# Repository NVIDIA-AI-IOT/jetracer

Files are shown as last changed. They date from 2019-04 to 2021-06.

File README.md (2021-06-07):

# JetRacer

> 6/01/2021 - JetPack 4.5.1 based image is updated. It is pre-configured for JetRacer. Detail [here](https://github.com/NVIDIA-AI-IOT/jetracer/blob/master/docs/software_setup.md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).



JetRacer is an autonomous AI racecar using NVIDIA Jetson Nano.  With JetRacer you will

* Go fast - Optimize for high framerates to move at high speeds

* Have fun - Follow examples and program interactively from your web browser

By building and experimenting with JetRacer you will create fast AI pipelines and push the boundaries of speed.

To get started, follow the [setup](#setup) below.

## Cars

There are two different JetRacer cars that you can build.  They differ primarily in size and speed.  Which one to pick depends on your use case

|  Latrax Rally | Tamiya TT02 |
|---|---|
|   |   | 
| 1/18th scale |  1/10th scale |
| Moderate Speed  |  High Speed  |
| ~$400 total build cost | ~$600 total build cost |
| Compact and portable |  Large and easy to modify |
| Soldering required |  No soldering required  |
| Base car pre-assembled | Base car assembly required |

If you have any questions, please reach out by [creating an issue](../..//issues).

## Examples

JetRacer comes with a couple examples to get you up and running.  The examples are in the format of Jupyter Notebooks, which are interactive documents which combine text, code, and visualization.  Once you've completed the notebooks, start tweaking them to create your own racing software!

### Example 1 - Basic motion

In this example you'll learn to progam JetRacer programatically from your web browser.  Learn more in the [examples](docs/examples.md) documentation.



### Example 2 - Road following

In this example, you'll teach JetRacer how to follow a road using AI.  After training the neural network using the [interactive training notebook](notebooks/interactive_regression.ipynb), you'll optimize the model using NVIDIA TensorRT and deploy for a live demo. Learn more in the [examples](docs/examples.md).



## Setup

To get started with JetRacer, follow these steps

1. Order parts from the bill of materials

    - [Latrax version](docs/latrax/bill_of_materials.md) 
    - [Tamiya version](docs/tamiya/bill_of_materials.md) 

2. Follow the hardware setup

    - [Latrax version](docs/latrax/hardware_setup.md) 
    - [Tamiya version](docs/tamiya/hardware_setup.md) 

3. Follow the [software setup](docs/software_setup.md)
4. Run through the [examples](docs/examples.md)

## See also

* [JetBot](http://github.com/NVIDIA-AI-IOT/jetbot) - An educational AI robot based on NVIDIA Jetson Nano

* [JetCam](http://github.com/NVIDIA-AI-IOT/jetcam) - An easy to use Python camera interface for NVIDIA Jetson
* [JetCard](http://github.com/NVIDIA-AI-IOT/jetcard) - An SD card image for web programming AI projects with NVIDIA Jetson Nano
* [torch2trt](http://github.com/NVIDIA-AI-IOT/torch2trt) - An easy to use PyTorch to TensorRT converter

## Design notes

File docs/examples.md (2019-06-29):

# Examples

Follow these examples to get started with JetRacer

> Ensure JetRacer is connected to WiFi and you've note the IP address as in the [software setup](software_setup.md)

## Example 1 - Basic Motion

In this example we'll show how to control JetRacer programatically from a web browser.

1. Navigate to ``http://<jetson_ip_address>:8888``

2. Sign in with the default password ``jetson``
3. Browse to the folder ``~/jetracer/notebooks`` in the Jupyter Lab file browser
4. Run through the notebook ``basic_motion.ipynb``

## Example 2 - Road Following

### Step 1 - Open the interactive trainer

1. Navigate to ``http://<jetson_ip_address>:8888``

2. Sign in with the default password ``jetson``
3. Browse to the folder ``~/jetracer/notebooks`` in the Jupyter Lab file browser
4. Open the notebook ``interactive_regression.ipynb``

### Step 2 - Run the trainer

>  You may want to use ``5W`` mode to prevent the Jetson Nano from drawing to much current and shutting down. Try opening a terminal and entering ``sudo nvpmodel -m1``.

1. In the cell *Task Definition* set ``TASK = 'road_following'`` to set the task name

2. Also set ``CATEGORIES = ['apex']`` to set the class names of the xy target category
3. Execute all of the remaining cells
4. Place the car in different positions, offsets and orientations along the track
5. Imagine the ideal path the car would follow in these positions overlaid on the camera feed
6. Click on the live camera feed as far along that ideal path as possible, such that the robot would not exit the track or collide with an object
7. Repeat this many times (say 50 to start)
8. Train the model for several epochs (say 10 to start) and see how the model performs
9. Iterate!  Try training a model, visualize the output in the live demo, find scenarios where the model is inaccurate and add data for those points, train again...
10. When you want to demo the model, save it to the path ``road_following_model.pth`` and restart the ``interactive_regression.ipynb`` notebook

### Step 3 - Run optimized live demo

1. Open and follow the notebook ``road_following.ipynb``

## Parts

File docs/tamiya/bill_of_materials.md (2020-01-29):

# Bill of Materials - Tamiya TT02

This page lists the parts needed to build JetRacer - Tamiya TT02 version.  After you've received the parts, follow the [hardware setup](hardware_setup.md).



## Jetson Nano

| Part | Quantity | Cost | URL | Notes |
|---|:---:|:---:|-----|---|
| Jetson Nano | 1 | $99.00 | [NVIDIA](https://developer.nvidia.com/buy-jetson?product=jetson_nano), [Amazon](https://amzn.to/2K36TPl) |  |
| Micro SD Card | 1 | $11.99 | [Amazon](https://amzn.to/2Mohzd1) | Must be at least 32GB |
| USB Battery | 1 | $13.99 | [Amazon](http://amzn.com/B07KPCKCYG/) | Must provide at least 5V @ 2A |
| USB A -> 2.1mm Barrel Cable | 1 | $7.00 | [Amazon](https://amzn.to/2SMmu8A) |  |
| 5V @ 4A Barrel Plug Power Supply | 1 | $14.95 | [Adafruit](https://www.adafruit.com/product/1466) | 2.1mm Iinner diameter |
| Jumper Caps Pack | 1 | $5.09 | [Amazon](https://amzn.to/2LP96QI) | 2.54mm pitch |

## Chassis

| Part | Quantity | Cost | URL | Notes |
|---|:---:|:---:|-----|---|
| RC Car | 1 | $118.99 | [Amazon](https://amzn.to/2LUn3gj), [Hobbytown](https://www.hobbytown.com/tamiya-nsx-tt02-4wd-on-road-tam58634/p508229), [Tamiya](https://www.tamiyausa.com/shop/110-4wd-shaft-drive-road-tt/rc-nsx/tt-02/) | Tamiya NSX TT-02 assembly kit
| Servo | 1 | $15.98 | [Amazon](https://amzn.to/2LS781O) | Futaba S3004 Standard Ball Bearing Servo |
| TX RX Combo | 1 | $129.99 | [Amazon](https://amzn.to/2yoyWC5) | Futaba 3PV 3ch 2.4GHz transmitter and receiver module set |
| RC battery pack | 1 | $39.99 | [Amazon](https://amzn.to/31330PW) | Tenergy 7.2V 3000mAh NiMH (2-pack) |
| RC battery charger | 1 | $20.99 | [Amazon](https://amzn.to/2GHi3ay) | Tenergy Universal RC Battery Charger |
| 3d-printed base board | 1 |  | [STL file](../../assets/tamiya_tt02/jetracer_tamiya_tt02_base_board.stl) | Can be printed purchased at [Donkey Car](https://store.donkeycar.com/products/nvidia-jetracer-3d-printed-parts) Store |
| 3d-printed camera mount | 1 |  | [STL file](../../assets/jetracer_cam_mount.stl) | Can be printed purchased at [Donkey Car](https://store.donkeycar.com/products/nvidia-jetracer-3d-printed-parts) Store |

## Jig

| Part | Quantity | Cost | URL | Notes |
|---|:---:|:---:|-----|---|
| 3d-printed jig plate | 1 |  | [STL file](../../assets/tamiya_tt02/jetracer_tamiya_tt02_drill_jig.stl) | to help drill holes on RC car chassis |

## Electronics

| Part | Quantity | Cost | URL | Notes |
|---|:---:|:---:|-----|---|
| PWM Servo Motor Driver | 1 | $6.99 | [Amazon](https://amzn.to/317xYqr) |
| RC Servo Multiplexer | 1 | $9.95 | [Pololu](https://www.pololu.com/product/2806) | |
| Servo Extension Cable Pack | 1 | $5.91 | [Amazon](https://amzn.to/2SMnkSM) | Male to Male, 10cm |
| Jumper Wire Pack | 1 | $6.98 | [Amazon](https://amzn.to/319x9NT) | Female to Female, > 10cm | |

## Wi-Fi

| Part | Quantity | Cost | URL | Notes |
|---|:---:|:---:|-----|---|
| Wi-Fi Card | 1 | $18.95 | [Amazon](https://amzn.to/319d6z3), [NewEgg](https://www.neweggbusiness.com/Product/Product.aspx?Item=9SIV21M85N2699) |  |
| Wi-Fi Antenna kit | 1 | $8.99 | [Amazon](https://amzn.to/2SPft6U) | IPEX MHF4 connectors |

## Camera

You need a wide angle camera for JetRacer.  Pick an option and order the parts listed.

### Option 1 - Wide angle Leopard Imaging camera

| Part | Quantity | Cost | URL | Notes |
|---|:---:|:---:|-----|---|
| Camera | 1 | $29 | [Leopard Imaging](https://leopardimaging.com/product/li-imx219-mipi-ff-nano/) | Select wide angle (**H145**) option |

### Option 2 - Raspberry Pi Camera V2 + Wide angle attachment

| Part | Quantity | Cost | URL | Notes |
|---|:---:|:---:|-----|---|
| Camera | 1 | $23.90 | [Amazon](https://amzn.to/2MSi6lL), [Adafruit](http://adafru.it/3099) | Raspberry Pi Camera V2 |
| Wide angle attachment | 1 | $18.99 | [Amazon(1)](https://amzn.to/2SPNKDu), [Amazon(2)](https://amzn.to/2SPOfgQ), [eBay](https://ebay.us/Fz7HGd) | 160-degree FoV |

## Assembly Hardware

| Part | Quantity | Cost | URL | Notes |
|---|:---:|:---:|-----|---|
| M3x45mm Standoff Pack | 1 | $10.69 | [Amazon](https://amzn.to/2LPuZ20) | To support 3d-printed base plate |
| M3 Universal Screw Pack | 1 | $12.94 | [Amazon](https://amzn.to/2LNGt6q) | 4x M3x8mm screws, 4x M3 flat head screws needed for 4 standoffs |
| M2x8mm Screw Pack | 1 | $6.39 | [Amazon](https://amzn.to/312PTOK) | Mounts accessories to 3D printed base plate.  18 screws needed per car |
| Battery Strap Pack | 1 | $6.98 | [Amazon](https://amzn.to/317zoRN) | 1 needed per car |

## Next

Follow the [hardware setup](hardware_setup.md).

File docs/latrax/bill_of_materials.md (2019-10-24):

# Bill of Materials

This page lists the parts needed to build JetRacer - Latrax Rally version.  After you've received the parts, follow the [hardware setup](hardware_setup.md).



## Jetson Nano

| Part | Quantity | Cost | URL | Notes |
|---|:---:|:---:|-----|---|
| Jetson Nano | 1 | $99.00 | [NVIDIA](https://developer.nvidia.com/embedded/buy/jetson-nano-devkit) |  |
| Micro SD Card | 1 | $13.99 | [Amazon](https://amzn.to/2Us6bOv) | Must be at least 32GB |
| USB Battery | 1 | $15.95 | [Amazon](https://www.amazon.com/5000-mah-Attom-Tech-Portable-Emergency/dp/B07MNWPFG8/) | Must provide at least 5V @ 2A |
| USB A -> 2.1mm Barrel Cable | 1 | $7.00 | [Amazon](https://www.amazon.com/gp/product/B075112RM6/) |  |
| 5V @ 4A Barrel Plug Power Supply | 1 | $14.95 | [Adafruit](https://www.adafruit.com/product/1466) | 2.1mm Iinner diameter |
| Jumper Caps Pack | 1 | $5.09 | [Amazon](http://amzn.com/B077957RN7/) | 2.54mm pitch |

## Chassis

| Part | Quantity | Cost | URL | Notes |
|---|:---:|:---:|-----|---|
| RC Car | 1 | $109.95 | [HobbyTown](https://www.hobbytown.com/traxxas-latrax-rally-1-18-4wd-rtr-rally-racer-green-tra75054-5-grn/p630138), [Amazon](http://amzn.com/B06W57XLRW) | Traxxas LaTrax Rally 1/18 4WD w/ 2.4GHz radio |
| 3d-printed base board | 1 |  | [STL file](../../assets/latrax_rally/jetracer_latrax_base_board.stl) | Can be printed purchased at [Donkey Car](https://store.donkeycar.com/products/nvidia-jetracer-3d-printed-parts) Store |
| 3d-printed camera mount | 1 |  | [STL file](../../assets/jetracer_cam_mount.stl) | Can be printed purchased at [Donkey Car](https://store.donkeycar.com/products/nvidia-jetracer-3d-printed-parts) Store |

## Electronics

| Part | Quantity | Cost | URL | Notes |
|---|:---:|:---:|-----|---|
| PWM Servo Motor Driver | 1 | $6.99 | [Amazon](http://amzn.com/B01D1D0CX2/) | PCA9685 |
| RC Servo Multiplexer | 1 | $9.95 | [Pololu](https://www.pololu.com/product/2806) | |
| Servo Extension Cable Pack | 1 | $5.91 | [Amazon](http://amzn.com/B00P6JJFIS/) | Male to Male, 10cm |
| Jumper Wire Pack | 1 | $6.98 | [Amazon](http://amzn.com/B01EV70C78/) | Female to Female, > 10cm | |
| Manual Override Switch Pack | 1 | $10.99 | [Amazon](https://www.amazon.com/gp/product/B07L74MMG8/) | |

## Wi-Fi

| Part | Quantity | Cost | URL | Notes |
|---|:---:|:---:|-----|---|
| Wi-Fi Card | 1 | $18.95 | [Amazon](https://amzn.to/2WKEkum), [NewEgg](https://www.neweggbusiness.com/Product/Product.aspx?Item=9SIV21M85N2699) |  |
| Wi-Fi Antennas | 2 | $5.06 | [Arrow](https://www.arrow.com/en/products/2042811100/molex) |  |

## Camera

You need a wide angle camera for JetRacer.  Pick an option and order the parts listed.

### Option 1 - Wide angle Leopard Imaging camera

| Part | Quantity | Cost | URL | Notes |
|---|:---:|:---:|-----|---|
| Camera | 1 | $29 | [Leopard Imaging](https://leopardimaging.com/product/li-imx219-mipi-ff-nano/) | Select wide angle (**H145**) option |

### Option 2 - Raspberry Pi Camera V2 + Wide angle attachment

| Part | Quantity | Cost | URL | Notes |
|---|:---:|:---:|-----|---|
| Camera | 1 | $23.90 | [Amazon](https://amzn.to/2MSi6lL), [Adafruit](http://adafru.it/3099) | Raspberry Pi Camera V2 |
| Wide angle attachment | 1 | $18.99 | [Amazon(1)](https://amzn.com/B07HMXJ9Y1), [Amazon(2)](https://amzn.com/B07HF81BVL/), [eBay](https://ebay.us/Fz7HGd) | 160-degree FoV |

## Assembly Hardware

| Part | Quantity | Cost | URL | Notes |
|---|:---:|:---:|-----|---|
| M2x6mm Screw Pack | 1 | $13.53 | [Amazon](https://www.amazon.com/gp/product/B01FXGHO2M/) | Mounts accessories to 3D printed base plate.  12 screws needed per car |
| M3x20mm Standoff Pack | 1 | $6.99 | [Amazon](https://www.amazon.com/dp/B072DVGWHZ/ref=cm_sw_su_dp) | Mounts 3D printed base plate to RC chassis. 4 standoffs needed per car |
| M2x38mm Screw Pack | 1 | $11.99 | [Amazon](http://amzn.com/B07CHJBK6F) | 2 needed per car |
| M2x30mm Screw Pack | 1 | $7.96 | [Amazon](https://www.amazon.com/dp/B015A31EVK/ref=cm_sw_su_dp) | 2 needed per car |
| Adhesive Pads Pack | 1 | $6.98 | [Amazon](https://www.amazon.com/gp/product/B001KYSAN4/) | 4 needed per car |

## Next

Follow the [hardware setup](hardware_setup.md).

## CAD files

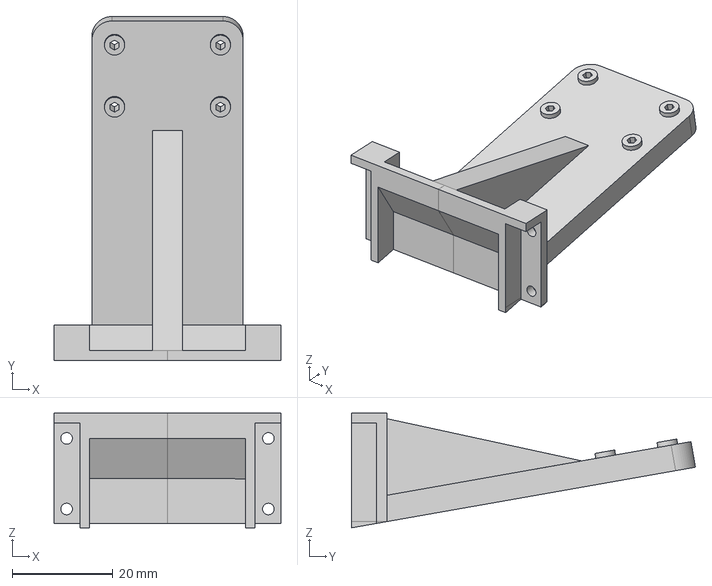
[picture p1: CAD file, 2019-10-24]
assets/jetracer_cam_mount.step
45.0 x 68.2 x 22.7 mm

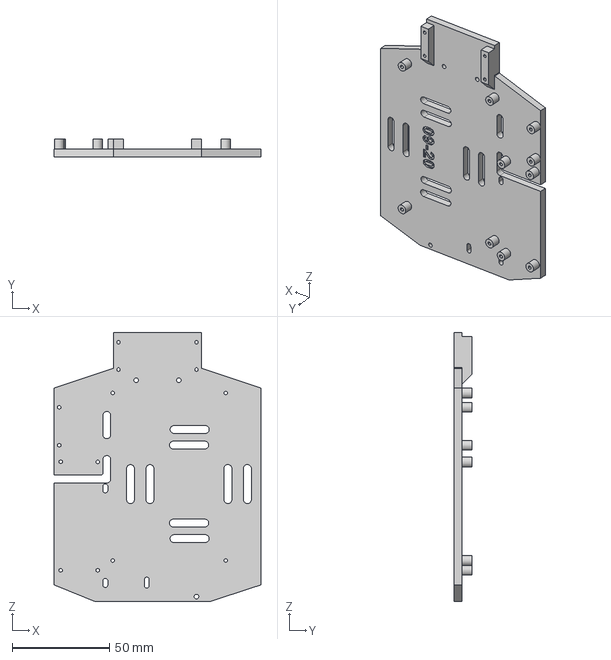
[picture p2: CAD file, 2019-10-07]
assets/latrax_rally/jetracer_latrax_base_board.step
106.0 x 9.00 x 138.0 mm

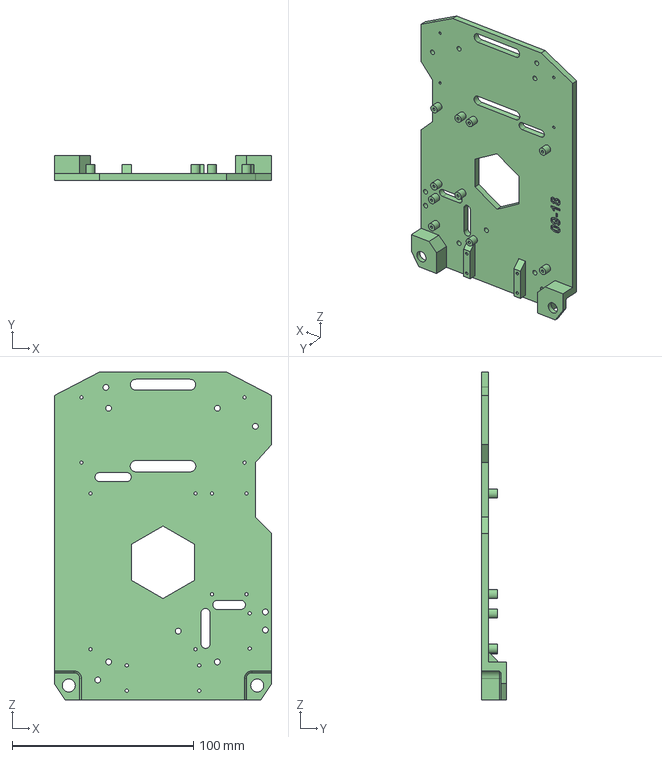
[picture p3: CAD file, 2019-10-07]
assets/tamiya_tt02/jetracer_tamiya_tt02_base_board.step
120.0 x 14.0 x 181.0 mm

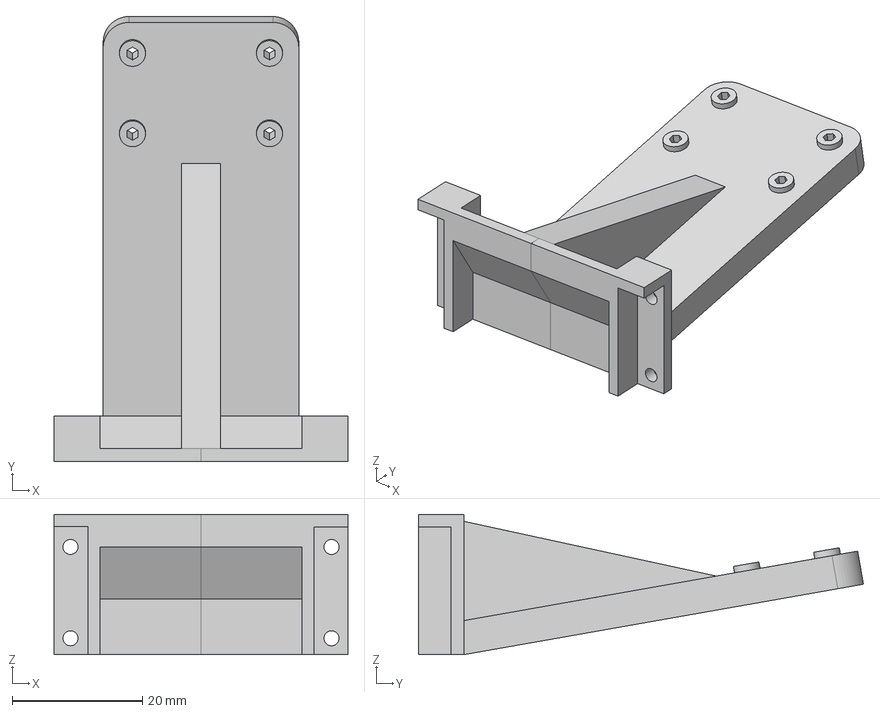
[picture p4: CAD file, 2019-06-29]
assets/latrax_rally/jetracer_latrax_cam_mount.step
45.0 x 68.2 x 21.5 mm

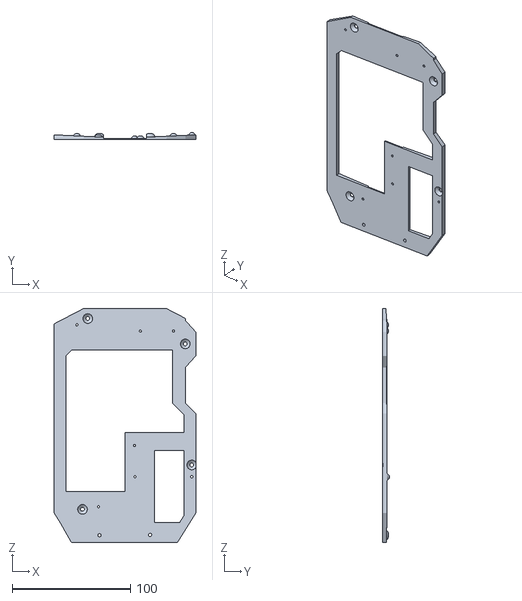
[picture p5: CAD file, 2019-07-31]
assets/tamiya_tt02/jetracer_tamiya_tt02_drill_jig.stl
120.0 x 6.00 x 198.0

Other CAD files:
assets/jetracer_cam_mount.iges
assets/jetracer_cam_mount.stl
assets/latrax_rally/jetracer_latrax_base_board.iges
assets/latrax_rally/jetracer_latrax_base_board.stl
assets/latrax_rally/jetracer_latrax_cam_mount.iges
assets/latrax_rally/jetracer_latrax_cam_mount.stl
assets/tamiya_tt02/jetracer_tamiya_tt02_base_board.iges
assets/tamiya_tt02/jetracer_tamiya_tt02_base_board.stl

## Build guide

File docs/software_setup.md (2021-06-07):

# Software Setup

> If you have built a 3rd-pary Jetracer kit (other than our DIY vehicles based on Latrax Rally or Tamiya TT-02), the following method (and the SD card images) may not work. <br> **Please check the manufacture's instruction on its kit's specific software setup.**

After finishing these steps, you'll be all set to program JetRacer.  Once you're finished, run through the [examples](examples.md).

## Step 1 - Flash micro SD card

1. Download a JetCard SD card image listed in below table onto a Windows, Linux or Mac *desktop machine*
2. Insert a 32GB+ SD card into the desktop machine
3. Using [Etcher](https://www.balena.io/etcher/) select the downloaded zip file and flash it onto the SD card
4. Remove the SD card from the desktop machine

### Latest Release (** **but not yet fully verified** ** )

> Please note, the password for the pre-built SD card is ``jetson``

| Platform | Board revision | JetPack Version | Download | MD5 Checksum |
| --- | --- | --- | --- |--- |
| Jetson Nano (4GB) | `A02` and `B01` | 4.5.1 |  [jetcard_nano-4gb-jp451.zip](https://drive.google.com/file/d/1aPbzQ0_Uja0jVD48oZUAuYYAz10JgbZu/view?usp=sharing) | 3195c91e6069c0418ec3c9736d130d01 |

### Old Release

> Please note that this image is only for the older `A02` revision of Jetson Nano board, which has only one camera (CSI) connector onboard.

| Platform | Board revision | JetPack Version | Download | MD5 Checksum |
| --- | --- | --- | --- |--- |
| Jetson Nano (4GB) | `A02` | 4.2|  [jetcard_v0p0p0.zip](https://drive.google.com/open?id=1wXD1CwtxiH5Mz4uSmIZ76fd78zDQltW_) | f7b635a651e4a2228e3812360cce74e3 | 

## Step 2 - Power on and connect over USB

1. Insert the configured SD card into the Jetson Nano module

2. Power on by plugging the USB barrel plug adapter into the USB battery pack
3. Connect your Windows, Linux, or Mac machine to the Jetson Nano via micro USB

4. On your Windows, Linux, or Mac machine, open a browser and navigate to ``192.168.55.1:8888``
5. Sign in using the default password ``jetson``

## Step 2 - Connect JetRacer to WiFi

1. Open a terminal in Jupyter Lab by clicking ``File`` -> ``New`` -> ``Terminal``

2. In the terminal, type the following command to list available WiFi networks, and find the ``ssid_name`` of your network.

    ```bash
    sudo nmcli device wifi list
    ```
3. Connect to  the selected WiFi network

    >  It should be on the same network that you will be webprogramming from

    ```bash
    sudo nmcli device wifi connect <ssid_name> password <password>
    ```
4. Note down the WiFi IP address (``inet``) of the WiFi interface ``wlan0`` returned by the following command.  We'll call this ``jetson_ip_address``
    
    ```bash
    ifconfig
    ```

## Step 4 - Connect to JetRacer over WiFi

1. Unplug the micro USB cable from the Jetson Nano

2. Close the previous Jupyter Lab browser tab
3. Open a new browser tab and navigate to ``http://<jetson_ip_address>:8888``
4. Sign in with the password ``jetson``
    
## Step 5 - Install Python packages

>  If you're using the latest JetCard image (targeting JetPack 4.5.1 or later), you can skip this step.  The latest JetCard image comes with these packages pre-installed.

1. Open a terminal and call the following to install the [JetCam](http://github.com/NVIDIA-AI-IOT/jetcam) Python package.

    ```bash
    cd $HOME
    git clone https://github.com/NVIDIA-AI-IOT/jetcam
    cd jetcam
    sudo python3 setup.py install
    ```
    
2. Execute the following command to install the [torch2trt](http://github.com/NVIDIA-AI-IOT/torch2trt) Python package

    ```bash
    cd $HOME
    git clone https://github.com/NVIDIA-AI-IOT/torch2trt
    cd torch2trt
    sudo python3 setup.py install
    ```
    
2. Execute the following in a terminal to install the [JetRacer](http://github.com/NVIDIA-AI-IOT/jetracer) package
 
     ```bash
     cd $HOME
     git clone https://github.com/NVIDIA-AI-IOT/jetracer
     cd jetracer
     sudo python3 setup.py install
     ```
 
## Step 6 - Set the Jetson Nano to 5W mode

To prevent the Jetson Nano from drawing more power than the battery can supply, we set it to 5W mode

1. Open a terminal and call the following to set 5W mode

    ```bash
    sudo nvpmodel -m1
    ```
    
## Next

Next, follow run through the [examples](examples.md).

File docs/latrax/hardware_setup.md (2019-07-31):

# Hardware Setup

Follow these instructions to build JetRacer - Latrax Rally version.  After you've finished, move on to the [software setup](../software_setup.md).

## Tools

* Phillips screwdriver set
* Hex screwdriver
* Soldering iron
* Drill with 3mm and 6mm drill bits
* Pliers
* Wire strippers

## Phase 1 - Car disassembly
### Step 1 - Remove shroud from car






1. Remove the 4 pins securing the shroud

2. Remove the shroud from the chassis

### Step 2 - Remove ESC and RC receiver from car










1. Remove the two screws securing the electronics hub to the chassis

2. Pry the electronics hub from the chassis
3. Remove the ESC and RC receiver from the electronics hub
4. Disconnect the two servo cables from the RC receiver
5. Remove the foam adhesive from the RC receiver

## Phase 2 - Car wiring
### Step 1 - Connect Jetson to servo driver






1. Select 4 female-to-female jumper cables from the bundle

2. Attach the jumpers to the servo driver pins ``VCC`` (white), ``SDA`` (gray), ``SCL`` (purple) and ``GND`` (black)
3. Attach the other end of the jumpers to the Jetson Nano pins ``3.3V`` (white), ``3`` (gray), ``5`` (purple) and ``GND`` (black)

### Step 2 - Connect servo driver to multiplexer








1. Connect channel ``0`` on the servo driver to channel ``S1`` on the multiplexer

    > Pay attention to the orientation of the cable for these steps!
    
2. Connect channel ``1`` on the servo driver to channel ``S2`` on the multiplexer

### Step 3 - Connect RC receiver to multiplexer










1. Connect channel ``3`` on the RC receiver to ``SEL`` on the multiplexer

2. Connect channel ``2`` on the RC receiver to ``M2`` on the multiplexer
3. Connect channel ``1`` on the RC receiver to ``M1`` on the multiplexer

### Step 4 - Connect multiplexer to ESC and servo








1. Connect the servo to ``OUT1`` on the multiplexer

2. Connect the ESC to ``OUT2`` on the multiplexer

## Phase 3 - Car assembly

### Step 1 - Mount ESC to base plate






1. Attach ESC to the base plate as indicated

    > Notice the two slots on the base plate for the ESC
    
2. Press down firmly to secure the ESC

### Step 2 - Mount RC receiver to base plate




1. Attach the RC receiver to the base plate as indicated

2. Press down firmly to secure the RC receiver

### Step 3 - Expose screw holes used to mount base plate







1. Remove the 4 screws indicated to expose holes used to mount the base plate

### Step 4 - Mount base plate to RC car










1. Select 4 ``M3x20mm standoffs``, 2 ``M2x38mm`` screws and 2 ``M2x30mm`` screws

2. Attach the base plate to the RC car chassis as indicated
3. Fasten the base plate using a hex screwdriver

### Step 5 - Route servo motor wire through base plate





> If the servo cable is not long enough to reach around the base plate, please route it as follows

1. Remove the servo cable from ``OUT1`` on the multiplexer that we attached previously

2. Route the servo wire through the slot base plate as indicated
3. Reconnect the servo cable to ``OUT1`` on the multiplexer

### Step 6 - Mount components to base plate







1. Select 10 of the ``M2x6mm`` screws

2. Fasten the multiplexer to the base plate
3. Fasten the servo driver to the base plate
4. Fasten the Jetson Nano to the base plate

### Step 7 - Connect WiFi card












1. Attach the two antennas to the WiFi card

2. Remove the Jetson Nano module from the developer kit board as indicated
3. Remove the M2 connector securing screw on the developer kit base board
4. Insert the WiFi card into the M2 connector slot
5. Reattach the screw to secure the WiFi card
6. Reattach the Jetson Nano module to the developer kit board

### Step 8 - Connect camera








1. Attach the camera to the Jetson Nano developer kit as indicated

    > Be careful when loosing the camera connector to not break it
    
2. Attach the camera mount to the base plate using 4 ``M2x6mm`` screws
3. Attach the camera to the camera mount using 4 ``M2x6mm`` screws

### Step 9 - Mount USB battery pack





1. Attach the USB battery pack to the underside of the base plate as indicated

### Step 10 - Attach USB barrel plug




1. Attach the 2 pin jumper to ``J48`` on the Jetson Nano developer kit to enable barrel plug power

2. Insert the barrel plug into the Jetson Nano developer kit

    > Before powering on, you'll need to follow the [software setup](../software_setup.md) to configure the SD card
    
## Phase 4 - RC transmitter modification

### Step 1 - Dissasmble radio










1. Remove the 5 screws securing radio halves with a phillips screwdriver

2. Peel off the radio stick joining the two halves
3. Place the radio sticker on one half of the radio
4. Remove the battery cover
5. Separate the radio into halves

### Step 2 - Remove trim / reset PCB





1. Remove screw securing the trim/reset PCB

2. Carefully sliding the wires out of the securing clip and pull the PCB to the side

### Step 3 - Drill hole for manual override switch





1. Mark the RC transmitter as indicated by the screwdriver tip

2. Using a ``6mm`` diameter drill bit, drill a hole through the marked location

### Step 4 - Drill hole for switch key






1. Temporarily insert the switch into the RC transmitter

2. Place the key washer on the other side of the transmitter
3. Mark the RC transmitter at the location of the screwdriver tip
4. Using a roughly ``2.5mm - 3.5mm`` drill bit, drill a hole through the marked location

### Step 5 - Fasten manual switch to RC transmitter







1. Re-insert the manual override switch into the hole

2. Place the keyed washer and nut back on the switch
3. Fasten the switch to the RC transmitter using pliers

### Step 6 - Solder switch to RC transmitter PCB










1. Cut the wires roughly at the length indicated

    > Ensure you cut the wires with enough length to reach the solder pads

2. Strip the wires as indicated
2. Apply solder to the two pads indicated
3. Apply solder to the stripped wire leads
4. Using pliers, hold the wires against the pads indicated and apply heat with the soldering iron

### Step 7 - Reassemble RC transmitter







1. Re-attach the halves of the RC transmitter

2. Fasten the halves using the original screws
3. Insert the 4 ``AA`` batteries, and apply the battery cover

## Hardware setup complete!



## Next

Next, follow the [software setup](../software_setup.md).

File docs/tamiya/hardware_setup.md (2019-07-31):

# Hardware Setup - Tamiya TT02

Follow these instructions to build JetRacer - Tamiya TT02 version.  After you've finished, move on to the [software setup](../software_setup.md).

## Tools

* Phillips screwdriver set
* Hex screwdriver
* Drill with 3mm and 6mm drill bits
* Countersink drill bit
* Pliers
* Wire strippers

## Phase 1 - TT-02 chassis setup
### Step 1 - Drilling mount holes to TT-02 chassis
> [Tips] It is better to perform this drilling before assembling the Tamiya TT-02 parts






1. Attach the jig on TT-02's "Lower deck" chassis ([Item #51532](https://www.tamiyausa.com/shop/spare-parts/rc-tt02-lower-deck/))

2. Align the jig to chassis holes. Use tapes to secure it
3. Use a ``3mm`` drill bit to drill 4 holes 

### Step 2 - Countersink 

> [Tips] Use of independent countersink drill bit (as opposed to the integrated one in the photo) is recommended.




1. Use countersink drill bit to make countersinks for flathead screw

2. Do this for all 4 holes

### Step 3 - Shaving motor cover




1. Use ``6mm`` drill bit to shave off part of motor cover part

2. Make sure it now has enough room for ``M3x45mm`` standoff to sit on the countersink hole you made on prior step

### Step 4 - Attaching standoffs on chassis 







1. Attach ``M3x45mm`` standoffs on "Lower deck" chassis with M3x8mm flat-head screws

2. Do this on all 4 holes
3. Do not tighten screws yet

## Phase 2 - Mounting components on base plate
### Step 1 - Multiplexer






1. Use 2x ``M2x8mm`` tapping screws to mount the multiplexier on the base plate

### Step 2 - Servo Motor Driver





1. Use 4x ``M2x8mm`` tapping screws to mount Servo Motor Driver on the base plate

### Step 3 - Jetson Nano Developer Kit





1. Use 4x ``M2x8mm`` tapping screws to mount Servo Motor Driver on the base plate

### Step 4 - IMX219 camera on Camera Mount





1. Use 4x ``M2x8mm`` tapping screws to attach camera to the camera mount

### Step 5 - Wi-Fi antennas







1. Place SMA anntena connector through the base plate hole

2. Put lock washer and split washer, and use the nut to tighten



## Phase 3 - Wiring

### Step 1 - Camera to Jetson Nano







1. Attach the camera to the Jetson Nano developer kit as indicated

    > Be careful when loosing the camera connector to not break it
2. Attach the camera to the camera mount using 4x ``M2x8mm`` screws
3. Attach the camera mount to the base plate using 4x ``M2x8mm`` screws

### Step 2 - Jetson Nano to Servo Motor Driver






1. Select 4 female-to-female jumper cables from the bundle

2. Attach the jumper wires to the Jetson Nano pins ``3.3V`` (red), ``3`` (orange), ``5`` (yellow) and ``GND`` (brown)
3. Attach the jumpers to the servo driver pins ``VCC`` (red), ``SDA`` (orange), ``SCL`` (yellow) and ``GND`` (brown)

### Step 3 - Servo Motor Driver to multiplexer





1. Connect channel ``0`` on the servo driver to channel ``S1`` on the multiplexer

    > Pay attention to the orientation of the cable for these steps!
2. Connect channel ``1`` on the servo driver to channel ``S2`` on the multiplexer

### Step 4 - Wi-Fi antenna to M.2 card





1. Attach the two antennas to the Wi-Fi card

### Step 5 - Wi-fi M.2 card to Jetson Nano










1. Remove the Jetson Nano module from the developer kit board as indicated

2. Remove the M.2 connector securing screw on the developer kit base board
3. Insert the Wi-Fi card into the M.2 connector slot
4. Reattach the screw to secure the Wi-Fi card

### Step 6 - USB Battery to Jetosn Nano







1. Attach the 2 pin jumper to ``J48`` on the Jetson Nano developer kit to enable barrel plug power

2. Insert the USB plug into the powerbank
3. Insert the barrel plug into the Jetson Nano Developer Kit
4. Use battery strap to fasten the battery on the base plate



### Step 7 - RX (RC receiver) to mulptiplexer






1. Connect ``CH3`` on the RC receiver to ``SEL`` on the multiplexer

2. Connect ``CH2`` on the RC receiver to ``M2`` on the multiplexer
3. Connect ``CH1`` on the RC receiver to ``M1`` on the multiplexer

### Step 8 - RC's ESC and servo to mulptiplexer 






1. Connect the RC servo to ``OUT1`` on the multiplexer

2. Connect the RC ESC to ``OUT2`` on the multiplexer

## Phase 4 - Final Assembly





1. Use 4x ``M3x8mm`` screws to attach base plates to the ``M3x45mm`` standoffs
2. Tighten the bottom flathead screws along with top ``M3x8mm`` screws
3. Attach the antenna to the SMA connectors

## Hardware setup complete!



## Next

Next, follow the [software setup](../software_setup.md).

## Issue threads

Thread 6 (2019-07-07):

Criteria for choosing the RC car

abhinav-upadhyay, 2019-07-07:
Hi,

This is not really an issue but a query. Did you choose the Traxxas LaTrax Rally car specifically for a particular reason, such as the 3d printed base board would fit well with it, or you knew that it was hackable? I am asking because the Traxxas RC cars are not available in India and importing it costs 3x more. There are other RC cars with similar specs (1:18 scale, 2.4 GHz radio, 4WD), such as [this](https://www.amazon.in/Sky-Zone-Waterproof-Controlled-Crawler/dp/B07JK3J437/).

The Donkey car is also a relatively affordable option. I would appreciate if you could give any opinion on this, I have never played with RC cars and haven't done any hardware hacking before.

tokk-nv, 2019-07-08:
Hi Abhinav,
Thank you for your question.

We chose Latrax Rally car mainly because it was hackable and small (being small is nice when it comes to demonstrating in a small space).
But you should be able to use other cars, as long as **they expose Servo and ESC controls through the standard 3-pin "Servo" connectors**.
So anything used in Donkey Car should work.

Our observation is that, once the RC car gets smaller than 1/10 scale, it uses what people call 3-in-1 controller, which combines the radio receiver (RX), the servo controller and the ESC in one unit.
This makes it very difficult to hack, as you cannot simply plug the cables from Servo and ESC to the PCA9685 board.
You can tell the car is using 3-in-1 design by finding the 5-wire cable coming out from the servo, like the one on Amazon you suggested.
Availability of the upgrade/replacement parts is also a good indication that the car is hackable.

I think you will have a better chance if you go for 1/10 scale and look in the hobby section rather than the toy section. (Perhaps you can find some relevant info on a forum like [this](http://www.rcindia.org/index.php)?)
I hope you will find a reasonably priced car for your project, and please share with us if you find a good one.

jasonlililililili, 2020-10-25:
May I ask which component has signal input and power output? Because I have no idea which component (RC reveiver? PCA9685? Servo Motor Driver? RC Servo? or the RC ESC?) should be connected to the battery.
Thank You!

krissdap, 2020-11-17:
Battery sends power to ESC.

In normal RC car, ESC connects to RC receiver, sends the power, and the receiver shares the power the steering servo connected to it.

In JetRacer, you have the servo multiplexer in the middle. And you power the Jetson Nano with USB power bank.

Of course you can also power each component in other ways if you are adventurous. :)

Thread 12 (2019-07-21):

VCC or V+?

zlite, 2019-07-21:
In this step of the instructions, you say to connect to VCC but the picture shows the connection to V+. Which is right?
https://user-images.githubusercontent.com/25759564/60315002-a56b1000-9919-11e9-8a53-2d941cc1b139.JPG

zlite, 2019-07-21:
If you plug it into V+ bad things happen! Nukes carrier board, wifi, etc. Yikes

jaybdub, 2019-07-21:
Hi Chris,

Thanks for pointing this out!  You're right, it's supposed to be VCC as stated.

We had this in right in an earlier shoot, I've updated to use the correct image.  You can find the change here

https://github.com/NVIDIA-AI-IOT/jetracer/blob/master/docs/hardware_setup.md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

Sorry for the confusion, I hope this didn't cause too much trouble.   Please reach out if you find anything else!

Thanks,
John

Closed 2022-07-18.

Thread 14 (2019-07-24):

Can you use C++ and ROS to control the car

ghost, 2019-07-24:
Seems you have to run Python via WIFI to control the car. What if you do not have WIFI? Can you run C++ and ROS to control the car?

jaybdub, 2019-07-27:
Hi Deeprun,

Thanks for reaching out!

>  What if you do not have WiFi?

You actually don't need WiFi.  This is a convenience so you can easily access the programming environment for rapid prototyping.  If you don't have WiFi, you can connect directly over micro USB, and access the web programming environment at ``192.168.55.1:8888``.  Or you could always open the a web browser on the Jetson Nano itself.  This would consume memory on the Nano though.

The examples are Jupyter notebooks (which require a web browser), but you can still operate the robot in plain Python (ie ``racecar.throttle = 0.3`` still works.

> Can you run in C++ and ROS to control the car?

We don't have a C++ library or ROS interface for JetRacer.  To create one, the primary effort would be in interfacing with the ``PCA9865`` servo driver chip to control the steering / throttle.  Perhaps there are C++ libraries (or maybe even ROS) for this purpose.

Please let me know if you have any other questions.

Best,
John

UberWagen, 2020-08-14:
> We don't have a C++ library or ROS interface for JetRacer. To create one, the primary effort would be in interfacing with the `PCA9865` servo driver chip to control the steering / throttle. Perhaps there are C++ libraries (or maybe even ROS) for this purpose.

Old thread, but I'm in the process of trying it. [This guy](https://github.com/dheera/ros-pwm-pca9685) did write a ROS driver for the 9865 if anyone finds this in the future.

Closed 2022-07-18.

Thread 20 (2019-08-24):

RC transmitter modification for tamiya version

hygradme, 2019-08-24:
Hi, I made JetRacer of tamiya version.

Then, I followed the instruction in [docs/examples.md](https://github.com/NVIDIA-AI-IOT/jetracer/blob/master/docs/examples.md) Example 1 - Basic Motion.
When I run the line of car.steering = 0.3 in [notebooks/basic_motion.ipynb](https://github.com/NVIDIA-AI-IOT/jetracer/blob/dev-stl/notebooks/basic_motion.ipynb), my car doesn't response.
The comment in the notebook said:
> If the car does not respond, it may still be in ``manual`` mode.  Flip the manual override switch on the RC transmitter.

However, my RC transmitter ( which is TTU-08 also in the photo of [docs/tamiya/bill_of_materials.md](https://github.com/NVIDIA-AI-IOT/jetracer/blob/master/docs/tamiya/bill_of_materials.md)) doesn't have override switch.

It seems like the hardware setup for latrax (at the Phase 4 of [docs/latrax/hardware_setup.md](https://github.com/NVIDIA-AI-IOT/jetracer/blob/dev-stl/docs/latrax/hardware_setup.md)) has RC transmitter modification.
Does tamiya version also have to do same modification like latrax version to make it ``manual`` mode?

romybompart, 2019-08-26:
Hi. I was reading, it uses channel 3 switch to change from manual to "Nvidia" mode.

Channel 3 is connected to SEL which is the input of the PIC10 at the PWM multiplexer. So that pin detects a pwn threshold to let channel M1 to M4 or S1 to S4 pass to OUT1 to OUT4 respectively.

In this manual you will see what is channel 3 switch:

manuals.hobbico.com › futPDF
Resultados de la Web
1M23N31504 - You have reached ftp.hobbico.com

If this does not work for you you can by pass the multiplexer and connect the PCA PWM driver ch0 to the steering wheel servo and ch1 to the ESC, but you won't have command on the car by your transmitter.

Let me know whatever you got.

hygradme, 2019-08-26:
Thank you for your advice.

I think I didn't have enough knowledge about RC transmitter.
My  [Tamiya RC Transmitter](https://www.amazon.com/Fine-Electric-Drive-Model-tamiya/dp/B0077K0WM2) has only 2ch which cannot send SEL signal to the receiver.

I bought combo version of NSX RC car with Tamiya TT02 and RC transmitter which is different from the one in [bill of materials](https://github.com/NVIDIA-AI-IOT/jetracer/blob/master/docs/tamiya/bill_of_materials.md).
I should have bought Futaba 3PV 3ch 2.4GHz transmitter.

As you told me, I bypass the multiplexer and switch "Nvidia mode" and "Manual mode" with just replacing the cable from RC transmitter with the one from motor driver by hand.
It is not convenient to replug cable every time after collecting data to switch to "Nvidia mode" but it works at least.

hygradme, 2019-09-01:
Sorry for late reply and thank you for your kind advice.
I followed your advice but I couldn't switch "Nvidia mode" and "manual" mode from ch2 of the driver.
As you mentioned, SEL may not receive valid signal from pca9685.
I cannot use oscilloscope right now so not sure the exact reason of this  but I will try the 2nd option which directly connects GPIO pins to SEL pin.

itsklee, 2020-06-20:
@romybompart @hygradme

I find the  way
pca96855 can  make signal  below

>   The multiplexer considers the RC signal on the SEL channel to be valid if it has a 10–330 Hz pulse
>   rate and 0.5–2.5 ms pulse width. The other inputs (S1–S4 and M1–M4) are unrestricted.
>

first follow @romybompart  's way
and  add some  code in
   class NvidiaRacecar(Racecar):

    def __init__(self, *args, **kwargs):
        super(NvidiaRacecar, self).__init__(*args, **kwargs)
        self.kit = ServoKit(channels=16, address=self.i2c_address)
        self.steering_motor = self.kit.continuous_servo[self.steering_channel]
        self.throttle_motor = self.kit.continuous_servo[self.throttle_channel]
        self.manual = self.kit.continuous_servo[self.manual_channel]

        **self.kit._pca.frequency= 100
        self.kit._pca.duty_cycle = 0x7fff**

and  then set  the  value

   car.manual = 0  #  will  control by  your trasmitter

or
   car.mamual = 1 #  will control  by your pca96855

thank you

abdul-mannan-khan, 2021-05-03:
I am having the same issue. I followed this method and my race car is still not moving.

Closed 2022-07-18.

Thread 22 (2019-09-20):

unable to train and run

gbr1, 2019-09-20:
Hi!
Just builded my Jetracer (latrax 1:18 -> [youtube video](https://www.youtube.com/watch?v=5ZBqgufzdm0) )
I created a setup track:
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
<br>
After following instructions:
1) _basic motion_ works correctly;
2) _interactive regression_ gives me always right-bottom blue point during "evaluation";
3) _road following_: car always go right.

I always tried with a simple path:
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
And car goes right.

Installed camera is: IMX219 with wide angle.

How do I choice correctly points?  Which is correct sequence (create images -> train button -> evaluate -> save)?
Is my track correct or are necessary other stuffs such as central line and uniform colours?

Thank you in advance!

jaybdub, 2019-09-25:
Hi gbr1,

Thanks for reaching out and sharing your video!  Very well done!

The track you created looks good to me, should certainly be able to work on that.  Hopefully we can get you up and running soon.

Could you provide the following information

1.  How many data samples did you collect / how was car placed?  (data variance is very important)
2.  How many epochs did you train for?  (it usually takes many, I'd guess at least 15+ to converge)

Best,
John

gbr1, 2019-09-28:
Hi @jaybdub!
I took about 200 photos and 3 epochs maybe that was the problem.
Then I moved on donkeycar software so I didn't try more.

Thank you.

RyanC1681, 2019-11-12:
Hi, John:
I took >200 photos but epoch always = 0 and car always do circle, not steering straight.
Could you give me a correct training sequence (live -> train button -> click left image -> count# inceasing -> evaluate -> save model)?
How to set another epoch or find out which point need more training/images?

Thanks

jaybdub, 2019-11-13:
Hi RyanC1681,

The work flow is generally to

1.  Collect images
2.  Train for several epochs until loss converges
3.  Run live to visualization how well the network is performing
5.  Repeat 1->3 until you are happy with the performance, at this point save the model

Please let me know if this helps.

Best,
John

ctye85, 2020-01-10:
Hi jaybdub,

I know this is a bit old, but perhaps you could help me out with my current situation if you have time.

I can get to the point where I'm consistently training a model that performs well after 100+ images and 15 or so epochs. It tracks movements around the track with a high degree of accuracy.

I essentially do exactly the work flow you described above: collect images, train for several epochs, and run it live to make sure the model is performing well. Rinse and repeat, then save the model when I'm satisfied.

However, when I attempt to run it with the Road Following notebook, it just turns in a continuous circle to the right. It does seem to adjust the degree of turning at times, which indicates that some commands seem to be going through.

Do you have any idea why this may be happening, considering the perceived accurate performance running the Interactive Regression notebook?

Thanks!

Closed 2022-07-18.

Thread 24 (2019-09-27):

any replacement for servo multiplexer?

nelsonjin, 2019-09-27:
Is there any replacement for servo multiplexer?
I can't buy it in my country...

tokk-nv, 2019-09-27:
Hi nelsonjin,
Unfortunately, as far as I'm aware right now, we don't find any good alternative to the Pololu servo multiplexer.
The servo multiplexer is just to add a safety feature, which allows you to stop the car when the computer or your code goes into an uncontrollable state.
So you can choose to just connect the PWM outputs from the PCA9685 breakout board directly to your servo and the ESC on your car, if you don't need that feature.

nelsonjin, 2019-09-29:
thanks, I'll try this with cautious

cygnusyang, 2019-11-08:
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

Hi tokk-nv,

I am trying to use nano to control the servos without the bluetooth receiver board. I found that the servo only can be controlled if I connect the bluetooth receiver board first. It seems that the bluetooth receiver is designed to negotiate with the servo control board.  I have tried to use oscilloscope to get the PWM output, the PWM output from PCA9685PW chipset is the same as CC26XX from the bluetooth receiver (about 100HZ). The GND and VOL(3.4v) also are the same. Do I need to send some signals to the servo control board before the PWM? Thanks.

larryw-jimi, 2022-02-18:
do we have any replacement now

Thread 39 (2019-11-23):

Tamiya version problem

xingtongli, 2019-11-23:
Hi,
I made a tamiya version. When I tried the basic motion part, the throttle command did not have any response from the car. I viewed an issue about the transmitter do not have manual override switch. So I bypass the multiplexer and connect the cable of servo motor and ESC to the PCA PWM driver directly. The steering command had response but the throttle did not have. My ESC's model number is TAMIYA TBLE-02S. What problems it might have? Thank you.

Ziegan, 2019-11-25:
I am also facing the same problem, while using the TAMIYA TBLE-02S ESC.
When bypassed to PCA PWM directly the steering command works....and the throttle dose'nt respond.
Is there any way to overcome this issue ?

Ziegan, 2019-11-25:
I have a TAMIYA build and all its necessary components that are stated in the billing informations for TAMIYA build.
My TAMIYA includes TBLE-02S ESC to control the motor.
The car doesn't respond while trying out the example basic motion,
So i tried out it with a different ESC - Jreleas F540 sensor-less motor ..., which also didn't work,
but when bypassed to the PCA PWM directly, the steering command works well with both the ESC's but the motor doesn't work.
Is there anyway to make this work ?
thanks.

Ziegan, 2019-11-25:
I have a TAMIYA build and all its necessary components that are stated in the billing information for JetRacer (TAMIYA build).
My TAMIYA includes TBLE-02S ESC to control the motor.
The car doesn't respond while trying out the example basic motion,
So i tried out it with a different ESC - Jreleas F540 sensor-less motor ..., which also didn't work,
but when bypassed to the PCA PWM directly, the steering command works well with both the ESC's but the motor doesn't work.
Is there anyway to make this work ?
thanks.

Ziegan, 2019-11-25:
Hello

**Goal** : I am Trying to Build JetRacer based on Tamiya Version .
I have bought all the Materials Mentioned in the Bill of Material of Tamiya based JetRacer

**Problem**: When Tried the Basic Motion, After making all the connections as per the  Build Instructions, The Car didn't Respond

**Options I have Tried**:
My TAMIYA includes TBLE-02S ESC( Speed controller)  to control the motor.The car doesn't respond while trying out the example basic motion,
So i tried out it with a different ESC - Jreleas F540 Brushless motor ..., which also didn't work,

When the  Polulu Multiplexer is not used when bypassed to the PCA PWM directly, the steering command works , But the Motor doesn't respond
Is there anyway to make this work ?

Ziegan, 2019-12-10:
Still waiting for any updates to overcome this problem !

jaybdub, 2019-12-11:
Hi All,

Thanks for reaching out, and terribly sorry for the delayed response!

Could you try inverting the throttle gain and then setting the throttle?

Perhaps,

```python
car.throttle_gain = -0.5
```

and then

```python
car.throttle = 0.5
```

As a safety precaution, make sure the car is suspended in the air.  It can go fast.

Please let me know if this works or not!  If it resolves the issue I will consider how to make this point clear.

Best,
John

tokk-nv, 2019-12-11:
Hi all,

In addition to what John suggested, it might help to put the motor ESC into Reverse Enabled mode.
It is possible that you are outputting PWM pulse to just apply "break" if the ESC is set to Reverse Disabled mode, so you want to flip the throttle_gain positive/negative in that case.

You can refer to TBLE-02S ESC manual for enabling reverse.
https://www.tamiyausa.com/media/files/45057ml-801-efb9.pdf

Ziegan, 2019-12-18:
Thanks for Your Help Guys..!
Finally my Tamiya Setup is working, it needs the throttle set up in negative for the car to move forward and positive to stop .., but my car can't get reverse !

Ziegan, 2019-12-28:
Recently,

I made another tamiya build using the list of materials shared in this page..,

While executing the program (basic_motion),
 i got this error...

Any suggestions to overcome this error

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

jaybdub, 2020-01-10:
@Ziegan

Glad to hear!  Did you set the ``throttle_gain`` to a negative value?

Did you follow the TBLE-02S ESC manual that @tokk-nv mentioned in previous comment.

Best,
John

itsklee, 2020-01-16:
Hello.
I'm making Tamiya version
The same thing is happening with Ziegan's problem.
Of course, jaybdub's comments were handled.
Negative processing of throttle_gain was applied, as well as the setting of Tamiya receiver.

By the way, when throttel is negative, moving forward,
If it is positive, it is operating as stop.
It does not work backwards.

Is there another way?

itsklee, 2020-01-19:
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

i’m found the solution
reverse move need more throttle gain
because receiver setting is forward full but reverse half or less

thank you

joessu, 2020-06-20:
I set my throttle gain to -1.0 to see what raw values would get me. 0.2 which is -0.2 was dead stop, no matter what the car was doing. Anything higher was move forward, anything less was move backward. Reverse is enabled on the speed controller.

Closed 2022-07-18.

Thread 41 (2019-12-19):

Receiver cable orientation

ChrisW0rk, 2019-12-19:
Hello, I have a question about the cable orientation in the final build.

The pictures in the build show the original 2 channel + B receiver, however it's unclear where the cables are supposed to be connected in the final build.

I can get the car running in Jupyter Lab, but when running the Basic Motion file, steering seems to control the car's throttle, and vice versa for throttle controlling the steering. In manual mode, the car controls as you would expect, this is only a problem for "Nvidia" mode.

Do you have any photos of the updated final build that would make the cable orientation more obvious? I feel like I must simply have wires in the wrong place or something.

Thanks a bunch!

tokk-nv, 2019-12-24:
Hello ctye85,

Given that you can correctly operate the vehicle in Manual mode, it sounds like you just need to flip the cables between your PCA9685 board and MUX board.

This shows the connection, and please note the channel 0 of the PCA9685 goes to S1 of MUX board, and channel1 of the PCA9685 goes to S2 of MUX board.
https://user-images.githubusercontent.com/25759564/62125310-a1684000-b281-11e9-99de-f458e6ca6b06.png

ctye85, 2019-12-24:
Thanks for clarifying. I actually tried this shortly after posting my original message and it worked like a charm. Cheers!

ctye85, 2019-12-25:
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

Thanks for your advice. Strangely enough, I had the cables in the orientation in your picture, but when I switched them to what's in my picture right now it actually works correctly! Even though it's reversed from what the instructions say.

Very curious...I wonder why that's the case. Anyway, your advice for flipping the cables still worked!

ctye85, 2020-01-03:
Hello again, I have a quick question about overall cable orientation.

It seems several things in my setup only work when they are done in reverse of what the GitHub page says.

For example, the above-mentioned channel 0 going to S2 and channel 1 going to S1 on the MUX. This is strange but it works, so I can't complain too much I guess.

Additionally though, Ch3 on the RC receiver goes to SEL on the MUX as usual. However, it works correctly if I connect CH2 on the RC receiver to M1 on the MUX, and CH1 to M2 on the MUX. Can you provide any insight as to why this may be the case? If it works then I'll keep it that way of course, I am just very confused about why that's the case.

Could it possibly be a hardware update issue, like since you made the build the MUX from the manufacturer has been slightly changed or something?

Thanks for any additional info you can provide!

Closed 2022-07-18.

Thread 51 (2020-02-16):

Replacing the Pololu 4-Channel RC Servo Multiplexer

zaher88abd, 2020-02-16:
Hello,

I am wondering if I can replace Pololu 4-Channel RC Servo Multiplexer with other chips. It is expansive to ship it to Canada. I don't have any experience with electronics, I appreciate any help.

krissdap, 2020-02-19:
Hi,

You can save cost by skipping the servo multiplexer but you will lose remote kill-switch as mentioned  here
[https://github.com/NVIDIA-AI-IOT/jetracer/issues/24#issuecomment-536114889](url)

zaher88abd, 2020-02-19:
Thank @krissdap for replay. Is that mean I can not connect TX RX Combo controller?

krissdap, 2020-02-20:
If you don't mind, you can manually connect-disconnect the servo and ESC wires, changing between your RX and the PCA9685.

That's the purpose of the servo multiplexer.

fariz, 2020-03-24:
yes i can t find it polulu multiplexer in my country, can you advice is there any replace component for polulu 4 channel

YaBr11, 2020-06-17:
Any Multiplexer with 2+ channels should work.

Keep in mind that the multiplexer also adds a safety level. If the ESC and the servo are "hard" wired to the PWM board without the Mulitplexer and the program crashes, the PWM will be continued with the last value, meaning the Jetracer driving uncontrollably with the last throttle and steering value.

That's why I would recommend using the multiplexer not only as a convenient feature, but also as a safety level in case of a software failure.

Closed 2022-07-18.

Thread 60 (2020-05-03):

Basic motion problems JetRacer

Traxan, 2020-05-03:
Hello everyone,

I had a problems with basic_motion notebook.
1. During calibration no matter what numbers I put in car.steering_gain and car.steering_offset my servo does not turn to right. Maximum motion to the right is natural straight run position (which should be on '0' value). Maximum left motion touches chassis and it looks like it would turn more down if there is not a chassis plate.
2. Second problem is about throttle. Contrariwise to the instinctive thinking, when I put negative value the car moves forward and opposite with positive value it moves backward.

Thank you in advance for any hints.
Greetings

krissdap, 2020-05-05:
For question 2, you can set throttle_gain to negative value, that way the throttle should behave in opposite direction.

cscscp, 2020-06-03:
I also encountered the same two problems. My workaround for problem 1 was detaching the servo wheel from the servo and reattaching it after setting the car.steering to 0.

ABilityConsult, 2020-06-08:
Basic Motion.¨
Problem 1: Throttle works only with negative values (not gain, but throttle)
I have not yet managed it to reverse.
Teleoperation.
Problem 1: The steering works, but here the throttle does not respond. Try to negate, but no response

YaBr11, 2020-06-17:
I had the same problem with the "wrong" direction of rotation of the motor.
Besides setting the throttle gain to a negative value, you can also switch two cables from the brushless motor to electrically change the direction of rotation. For me this was the better fix, because my ESC internally reduced the reverse throttle. This led to a much faster reverse speed, than the normal speed with the software fix.

With some ESCs you can also change the direction of rotationin the ESC settings, but I haven't tried that yet.

DeepLJoerg, 2021-03-19:
Please note the throttle is directly mapped to the RC car.  When the car is stopped and a negative throttle is set, it will reverse.  If the car is moving forward and a negative throttle is set, it will brake.

pbalbastre, 2021-04-14:
> I also encountered the same two problems. My workaround for problem 1 was detaching the servo wheel from the servo and reattaching it after setting the car.steering to 0.

How do you do this? I'm having the same problem, throttle works fine but steering only moves a little bit the first time and after that is not moving anymore.

DeepLJoerg, 2021-04-14:
> > I also encountered the same two problems. My workaround for problem 1 was detaching the servo wheel from the servo and reattaching it after setting the car.steering to 0.
>
> How do you do this? I'm having the same problem, throttle works fine but steering only moves a little bit the first time and after that is not moving anymore.

I have had the same problem. If your steering does not work anymore, what is the display at the Jetracer showing?
Mine went black, so the servo must have been crashed. I detached the servo and no problem occurred - e.g. motherboard works.
A new servo solved the problem, no everything is fine.

Please consider that the servo may be corrupt.

pbalbastre, 2021-04-14:
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

The steering moves in C++ but not in Python.

DeepLJoerg, 2021-04-15:
> The steering moves in C++ but not in Python.
What is the OLED display at the Jetracer saying in Python and in C++. Any difference?

pbalbastre, 2021-05-04:
Sorry for the late reply. The screen is showing usual info both in Python and C++. No difference.

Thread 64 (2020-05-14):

Upgrade to Jetson Xavier NX

dsvua, 2020-05-14:
I would like to upgrade to Jetson Xavier NX dev board. However, it requires 19v power and I am not sure how to proceed. Is it possible to document upgrade path to Jetson Xavier NX and what are our hardware options? Should we use Nano board with NX module instead of NX dev board? I would like to use Jetson Xavier NX board as it has build in wireless and separate M2 slot for SSD and I do not need to share USB port between SSD hard drive and Intel Realsense D435i camera.

dsvua, 2020-05-15:
I guess, upgrade to 3S Lipo battery will work, but will require motor and ESC replacement as well as adding some power split (between ESC and Jetson) board. 3S Lipo battery has voltage 9-12v and, technically, should be enough. Is there a better way?

YaBr11, 2020-06-17:
I also evaluated different power supply options when upgrading to the Jetson Xavier NX.
First thing that came to my mind was also using the Lipo battery, but you already mentioned the drawbacks. Another problem with this approach is the completely missing BMS. So neither the Jetson is protected from overcurrent/overvoltage nor is the battery protected from deep discharge in case you forget to turn off the Jetson.

But there are Powerbanks designed for Laptops that can deliver 12 V and over 60 W. That's the solution I'll go with.

maximveksler, 2020-08-07:
Not an electrical engineer. Interested in building the hardware and playing with the Model.

Would appreciate an upgrade path to Xavier NX

outbackdingo, 2020-09-22:
the xavier can run from 12V also... you dont need 19v.... add a DC-DC NUC power supply / openups2 from mini-box.com

gmanwork, 2020-10-24:
folks, i have been living through the Xavier upgrade for past few months. the sd card image doesn't boot (probably because it is meant for Nano). and manual install also have a bunch of issues due to different jetpack/libraries and almost every module being preinstalled with deprecated tools. i'm still building stuff from source and not gotten to the end of the tunnel yet...
anywhoooo... the power bank thing is another thread in my story. i hope some of my learning can help others...
the 5.2mm barrel jack on Xavier is a standard interface and any power bank meant for laptops with same jack or converter would work since most all laptop PSUs are 19v and 3A or more so the power banks for laptops are quite suitable for Xavier. with that said, most of the power banks available are quite expensive ($100 or more).
one cheaper alternative is to use battery packs that take 4 or more lipo cells (you have to buy the enclosure and cells separately). many available online ([link](https://www.ebay.com/sch/i.html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)). the Cons for this alternative is weight of the package might be 1.2-2lb or more.
the only suitable but not readily usable option i found was Dell power companion PW7015 ($45 at Staples). it provides 19v, with 12Ah capacity / 65W and around 1lb weight. problem with this one is the stupid dell propitiatory center pin interface which is used for communication from laptop to PSU/power bank to tell it how much volts are needed (and to not charge laptop battery if the PSU / source is below the laptop's expected wattage rating). the power bank shuts down after 30sec.
i'm working on a hack to spoof it by sending the expected signals (1-wire - ATTINY85 board) but no luck yet...

just wanted to share all my research so we can collectively move forward :)

Closed 2022-07-18.

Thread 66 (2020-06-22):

Jetracer Built Using Waveshare AI Kit Not Moving Forward

ArjunGupte1, 2020-06-22:
Hello,
My Waveshare Jetracer Kit (found here: https://www.waveshare.com/wiki/JetRacer_AI_Kit) is not responding to the car.throttle command in the basic_motion jupyter notebook. It is responding fine to the steering commands sent to the servo at the front, but regardless of the throttle value/gain sent to the rear motors, they are not spinning.

Help on how to debug or suggestions for how to address this problem would be appreciated.

Thanks

openbsod, 2020-06-23:
Hello.

1:1 same problem with Waveshare Jetracer Kit with jetson nano rev A02. Steering works fine, throttle does not work.

Every notebook start

`>>> from jetracer.nvidia_racecar import NvidiaRacecar
>>> car = NvidiaRacecar()
`

produce these errors

`Jun 23 10:29:14 jetson kernel: tegra-i2c 7000c400.i2c: pio timed out addr: 0x40 tlen:0 rlen:0
Jun 23 10:29:14 jetson kernel: tegra-i2c 7000c400.i2c: --- register dump for debugging ----
Jun 23 10:29:14 jetson kernel: tegra-i2c 7000c400.i2c: I2C_CNFG - 0x22c00
Jun 23 10:29:14 jetson kernel: tegra-i2c 7000c400.i2c: I2C_PACKET_TRANSFER_STATUS - 0x10001
Jun 23 10:29:14 jetson kernel: tegra-i2c 7000c400.i2c: I2C_FIFO_CONTROL - 0xe0
Jun 23 10:29:14 jetson kernel: tegra-i2c 7000c400.i2c: I2C_FIFO_STATUS - 0x800080
Jun 23 10:29:14 jetson kernel: tegra-i2c 7000c400.i2c: I2C_INT_MASK - 0x7c
Jun 23 10:29:14 jetson kernel: tegra-i2c 7000c400.i2c: I2C_INT_STATUS - 0x2
Jun 23 10:29:14 jetson kernel: tegra-i2c 7000c400.i2c: i2c transfer timed out addr: 0x40
`

Thank you in advance.

openbsod, 2020-06-23:
Been there with same issue.

Somehow I found myself with https://github.com/NVIDIA-AI-IOT/jetracer installed instead of  https://github.com/waveshare/jetracer

After proper software was installed troube had gone. Throttle works fine for now.

ArjunGupte1, 2020-06-23:
Thanks for the response. I will try making the change you had suggested and see if the throttle works then. But how did you uninstall the original GitHub repository from the Jetson Nano and then reinstall the new one?

openbsod, 2020-06-23:
I didnt do that.

cd ~/jetracer

```
git remote -v
origin	https://github.com/nvidia-ai-iot/jetracer (fetch)
origin	https://github.com/nvidia-ai-iot/jetracer (push)
```
jetson@jetson:~/jetracer$ **git remote set-url origin https://github.com/waveshare/jetracer**
```
jetson@jetson:~/jetracer$ git remote -v
origin	https://github.com/waveshare/jetracer (fetch)
origin	https://github.com/waveshare/jetracer (push)
```

and sudo python3 setup.py install

chealyte, 2020-06-30:
Hi guys sorry to hijack topic but it seems we got some users of waveshare here. I am really a noob when come to this AI and python.

i am in same problem I could not get car to move forward. I use waveshare repo. I try teleoperation however I can only get it to turn left and right while the car stand still I could not get it to move ..

mipsan, 2020-07-06:
@ArjunGupte1,

Did you resolve this issue?

My JetRacer also responds for steering controls but does not for throttle.

ArjunGupte1, 2020-07-06:
Yes, sorry for the late response but after using openbsod's fix it worked. You need to use the forked waveshare repository, not the main Nvidia one. After following his steps remember to close and restart the kernel manually in jupyter notebooks before running the new code (or else your old code will keep running and the new code won't get deployed to the jetson nano).

mipsan, 2020-07-07:
Thansk, @ArjunGupte1,

I tested as you said and got same result.
I installed from jetcard to jetracer as here: https://www.waveshare.com/wiki/JetRacer_AI_Kit

When I assign some value to car.throttle, Jetracer makes some noise.
And clear by zero, noise is disappeared.

Now, I'm gonna try from the first, microSD image file again.

mipsan, 2020-07-07:
@ArjunGupte1

Nothing! Even I did microSD image job.
Do you have any info about this DC gear motor? e.g vendor

It does not move with direct power feeding by power supply.
12V.

mipsan, 2020-07-07:
@ArjunGupte1

I found out what's wrong.
DC Geared motor itself!
Spin motor shaft couple of minutes by hand without power feeding.
And it runs -_-;;

Very embarrassed!

Thanks,

FortyLuck, 2021-06-05:
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

This approach works for me, thanks!

mipsan, 2021-06-07:
https://www.youtube.com/watch?v=5ZMW_KMenio&t=3s

Short video clip here.
I made s short guide book which includes JetRacer, OpenCV and Jetson specific deep learning examples.
With this, to my surprise, some undergraduate guys made this !

TigroTigro, 2021-06-08:
Any ideas what else may be causing problems with Waveshare? I've tried the solution provided by @openbsod but to no avail, sadly :/ Whether it be on the Nvidia or the Waveshare branch, I can run the movement commands with no errors, I can print values of the car's parameters too but it still does not make it move:

```
>>> from jetracer.nvidia_racecar import NvidiaRacecar
>>>
>>>
>>> car = NvidiaRacecar()
>>> car.steering = 0.3
>>> print(car.steering_gain)
-0.65
>>> print(car.steering_offset)
0.0
>>> car.throttle = 0.2
>>> print(car.throttle_gain)
0.8
>>> car.throttle_gain = 0.5
>>>
```

I've checked the connections a couple times and everything seems perfectly as per the instructions (I have the AI Pro kit). The only thing I did _not_ do was connecting the Wifi/Bluetooth module cause in my 2GB Nano there is no extension card slot under the radiator like in the other versions so I bypassed that by having a wifi adapter plugged into the USB port of the Nano - and it works perfectly fine establishing the connection. The only thing that baffles me is that the onboard LCD of the Waveshare board (the one that also holds the batteries) does not ever light up - it'd be weird for it to have power problems considering that the power is passed to the Nano so I don't know whether it plays a role here but I'm mentioning it just in case. Thoughts? :(

Closed 2022-07-18.

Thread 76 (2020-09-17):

Collision Avoidance and Object Following on Jetracer

abuelgasimsaadeldin, 2020-09-17:
Hi, has anyone tried collision avoidance or object following on the Jetracer? I have worked on those with my Jetbot and would like to do the same with my Jetracer but not sure how. Any help would be much appreciated. Thanks!

abuelgasimsaadeldin, 2020-09-18:
Update:
I have managed to collect collision avoidance data into my Jetracer and have successfully trained the model using codes similar to Jetbot. However when trying to run the live demo on my Jetracer, when running the last line "camera.observe(update, names='value')" I get the following error:

Exception in thread Thread-4:
Traceback (most recent call last):
  File "/usr/lib/python3.6/threading.py", line 916, in _bootstrap_inner
    self.run()
  File "/usr/lib/python3.6/threading.py", line 864, in run
    self._target(*self._args, **self._kwargs)
  File "/usr/local/lib/python3.6/dist-packages/jetcam-0.0.0-py3.6.egg/jetcam/camera.py", line 34, in _capture_frames
    self.value = self._read()
  File "/usr/local/lib/python3.6/dist-packages/traitlets/traitlets.py", line 584, in __set__
    self.set(obj, value)
  File "/usr/local/lib/python3.6/dist-packages/traitlets/traitlets.py", line 573, in set
    obj._notify_trait(self.name, old_value, new_value)
  File "/usr/local/lib/python3.6/dist-packages/traitlets/traitlets.py", line 1205, in _notify_trait
    type='change',
  File "/usr/local/lib/python3.6/dist-packages/traitlets/traitlets.py", line 1210, in notify_change
    return self._notify_observers(change)
  File "/usr/local/lib/python3.6/dist-packages/traitlets/traitlets.py", line 1247, in _notify_observers
    c(event)
  File "<ipython-input-12-4d7cee41da0b>", line 18, in update
    car.throttle = -0.4
  File "/usr/local/lib/python3.6/dist-packages/traitlets/traitlets.py", line 584, in __set__
    self.set(obj, value)
  File "/usr/local/lib/python3.6/dist-packages/traitlets/traitlets.py", line 573, in set
    obj._notify_trait(self.name, old_value, new_value)
  File "/usr/local/lib/python3.6/dist-packages/traitlets/traitlets.py", line 1205, in _notify_trait
    type='change',
  File "/usr/local/lib/python3.6/dist-packages/traitlets/traitlets.py", line 1210, in notify_change
    return self._notify_observers(change)
  File "/usr/local/lib/python3.6/dist-packages/traitlets/traitlets.py", line 1247, in _notify_observers
    c(event)
TypeError: 'int' object is not callable

Anybody knows how to overcome this problem?

chealyte, 2020-09-18:
it would be nice if we can implement it here too but sure if jetson nano have power to process road following and object avoidance at high speed or not since it seem at max processing power already.

Closed 2022-07-18.

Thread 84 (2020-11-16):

Jetracer doesn't respond to steering and throttle settings in Python code

zhousean, 2020-11-16:
Bought all Tamiya parts and assembled them this summer. Was going through the software set up, but can't really run basic_motion.ipynb. For example, when I run the following lines of code, the car has no response.

NvidiaRacecar().steering = -0.2
car.throttle = 0.5

The car drives fine with the Futaba remote control, forward/reverse and steering. It just doesn't respond to the Python code.

I looked into the hardware setup. RC's CH1/CH2 connect to M1/M2 on the multiplexer and Servo driver CH1/CH2 to S1/S2 on the multiplexer. And RC's CH3 connects to SEL on the multiplexer. If I turn CH3 over 60% on the Futaba RC, sometimes the car will respond to the Python steering/throttle instructions but very inconsistently and in most cases it still doesn't work.

Anyone can shed some light here? I have to admit this is my first time to play with Servo/RC/Multiplexer/Jetson nano. I probably have missed something very basic here.

jreinmuth, 2020-11-16:
Hi,

do you have tried to set other values for steering and throttle in the jupyter notebook as well ?
I also had some issues with my setup (T3PV mit R304SB and brushed motor). You can try setting CH3 to 100% - this is just the kill-switch if AI is going mad :-), so it is on/off -> 0/100%

zhousean, 2020-11-17:
Thanks @jreinmuth. By "Python code", I meant Jupyter notebook code. I am trying basic_motion.ipynb. For me, setting CH3 to 50% seems to be the sweet spot. If I set CH3 to 0%, T3PV RC takes full control. If I set CH3 to 100%, neither T3PV RC nor Jetson Nano controls the steering and throttle.

krissdap, 2020-11-17:
How do you set CH3 to 60%?
Like @jreinmuth stated, CH3 from the radio supposed to either send full 100 or 0, not something in between.

The multiplexer would either forward signal from Futaba receiver or from the servo driver, depends on that signal.
May be it's some kind of trimming on your radio that makes it work that way?

Or is it possible that the multiplexer is faulty? If you can try connecting from the PWM driver directly to the ESC / Servo, see how that work out.

zhousean, 2020-11-20:
T3PV RC allows me to set CH3 incrementally from 0-100% by pressing + or - button.
I also tried to bypass multiplexer by connecting Servo Motor Driver to ESC/Servo. It behaves very similarly. The car responds to steering setting but in most cases there is a couple of seconds delay. The car doesn't respond to most throttle settings but responds to some randomly. Really puzzling.

jreinmuth, 2020-11-20:
I also had some issues first. Steering was ok, but ESC did not work with the standard setting. Check if ESC mode is set to correct values for brushed or brushless motor. If this is set correct, you can check if you'll get your car running with the values I have set https://github.com/jreinmuth/jetracer/blob/master/jetracer/nvidia_racecar.py
ESC behaviour is not necessarily linear - reverse mode needs higher values to get a movement.
P.S. Just to check - You set the values , saved them for your configuration on T3PV and then you have this config up and running and you have used the switch on the right side of T3PV to turn remote control off and give control to Jetson, right ?

krissdap, 2020-11-21:
@zhousean thanks for clarifying that up.

For throttle, I think you should try changing throttle_gain and throttle_offset value.
TBLE02S ESC has Forward/Brake/Reverse functions, which makes it respond differently on some commands.

Also, just to confirm the direction, ESC yellow wire goes to motor yellow wire, ESC blue wire goes to motor green wire.

zhousean, 2020-11-22:
Thanks @jreinmuth @krissdap I will try to the throttle_gain and throttle_offset and let you know how it goes.
In terms of wiring, I assume mine is correct because if I set CH3 to 0%, I can drive the car fine with RC, forward, reverse, and steering?

zhousean, 2020-12-03:
tried to change the throttle_gain and throttle_offset values but they didn't do anything to change the behavior.

@jreinmuth was reading your question below in your details. I don't think I am doing all those steps with T3PV. Also the switch on the right doesn't really do anything, i.e. it doesn't turn off/on the RC. Any specific documentation that I should read?

P.S. Just to check - You set the values , saved them for your configuration on T3PV and then you have this config up and running and you have used the switch on the right side of T3PV to turn remote control off and give control to Jetson, right ?

jreinmuth, 2020-12-03:
hi, did you also have seen this comment in my file "#after changing values, re-run setup.py" without this, settings are saved but not active as the old instance is used.

for the settings in T3PV, just press the button with arrow on the right side until "SYS" then check if there is value of -100% set for ch3 then move on with the arrow button until you reach "Copy", there I have stored theses settings to 1 (I think it was pressing + and - together until it beeps (i'm not 100% sure right now, so check operations manual of T3PV). then once again arrow button 1 time and you're back in main menu. now you can toggle the switch on right side to turn on/off "jetson control"

With that settings, you should be able to drive the car either fully managed by RC or by Jetson. If not, check wiring and jumpers

MHaz42, 2021-02-28:
Hi, I have the same problem, my steering and throttle doesn't respond to python code but controller works just fine.
Unfortunatly I haven't bought the same controller as the instructions said because it wasn't available in my country.
Maybe it is because of that ?
Can someone help me ?

MB

MounaSamaali, 2023-08-23:
hello, I'am starting controlling the jetracer for the first time. However Jetracer doesn't respond to steering and throttle values coded in python with these lines :
car.steering = 0.4
car.trottle =0.2
and also the jetracer dose not respond to the gamepad mouvements, I had theses errors on coding.

_### **[IndexError                                Traceback (most recent call last)
<ipython-input-35-28921d6c799e> in <module>
----> 1 left_link = traitlets.dlink((controller.axes[1], 'value'), (car, 'steering'), transform=lambda x: -x)  # link controller 0.5 * controller axes 0 value to car steering
      2 right_link = traitlets.dlink((controller.axes[5], 'value'), (car, 'throttle'), transform=lambda x: -x)  # link 0.3 * axes 1 value to throttle**_

please any help for controlling the movement of the jetracer,

Thank you in advance
Mouna SAMAALI
IndexError: tuple index out of range
]([url](

> url

))

Closed 2022-07-18.

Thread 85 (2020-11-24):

Jupyter Lab widget.Controller instead of RC controller

feldiaz, 2020-11-24:
While trying to dlink the widget.controller to the car.steering values as:
steering = traitlets.dlink((controller.axes[1].value, 'value'), (car.steering, 'value), transform = lambda x:-x)
I do have the following error:
"Each object must be HasTraits, not <class 'float'>"
I had created a __init__ def on racecar.py to assure that steering and throttle are traitlets but no luck there.
I am having issues with my RC controller so I am trying to get the Jupyter Lab widget.Controller to communicate with the Adafruit ServoKit library and be able to generate some data for training.
I am aware that Jetbot manage the dlink between controller and DC motor without issues. is there anything different in Jetracer that prevents that?
I appreciate the help.

mvshalamov, 2020-11-29:
you should to understand how the traitlets library works (https://traitlets.readthedocs.io/en/stable/).

in your case you can do this:

```
import traitlets
from traitlets import HasTraits, observe

class Move(HasTraits):
    ax1 = traitlets.Float(default_value=1).tag(config=True)

    @observe('ax1')
    def _observe_ax1(self, change):
        car.steering = change['new']

m = Move()

traitlets.dlink((controller.axes[1], 'value'), (m, 'ax1'), transform=lambda x: -x)
```

feldiaz, 2020-11-29:
Hello Maxim,
Thanks for the info.
Unfortunately solution stills not working.
**All below listed code works:**

_import ipywidgets as widgets
import traitlets
from traitlets.traitlets import link, dlink, HasTtraits, observe
controller = widgets.Controller(index=0)
display(controller)_

To test the dlink feature:

_w=widgets.FloatSlider(value=1, min = -1, max=1, step=0.01)
test_dlink = traitlets.dlink((controller.axes[1],'value'), (w, 'value'), transform = lambda x:-x)_

To test the ServoKit library:
(Car steering servo is positioned depending on the controller position, but only one time. I need to re-run the cell to get the steering servo to a new position)

from adafruit_servokit import ServoKit
steering_servo = ServoKit(channels=16)
steering_arm = steering_servo.continuous_servo[1]
steering_arm.throttle = controller.axes[1].value_

All above code works.

**Below code does not produce any physical movement:**

from jetracer.nvidia_racecar import NvidiaRacecar
car = NvidiaRacecar()
class Move(HasTraits):
    ax1 = traitlets.Float(default_value=1).tag(config=True)

    @observe('ax1')
    def _observe_ax1(self, change):
        car.steering = change['new']

m = Move()

direction = traitlets.dlink((controller.axes[1], 'value'), (m, 'ax1'), transform=lambda x: -x)_

Something seems to be broken between widgets.Controller and its ability to connect to the ServoKit library. What is intriguing is that for DC motors, Nvidia Jetbot seems to got it working.

Closed 2022-07-18.

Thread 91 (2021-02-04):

The problem of not booting when burning jetcard image to sd card

Choikyungho9, 2021-02-04:
jetcard (OS) state seems odd.

I put jetcard_v0p0p0.zip onto the sd card and attached it to the jetson nano.

when i burn jetcard to SD card, there is a problem that booting is not possible.

Only ndivia is displayed and it does not boot.

Are there other versions of jetcard?

please help me.

jsopdebeeck, 2021-02-07:
Same here. The image is not working.

Rafipaulino, 2021-02-17:
Has somebody fixed this problem? I have the same.

TomasVraspir, 2021-02-18:
I have the same problem. Does it have a solution?

jsopdebeeck, 2021-02-18:
Hello, I solved the issue by replacing the CPU unit with an other one (same , B01), then everything started well. Or check that your CPU unit is 100% clean and well plugged.

grahil247-code, 2021-02-22:
Not sure that would fix the issue. Swapping out another CPU from the same board shoe that this is possibly a firmware / driver issue. I have the same problem so something must have changed for this not to work. Hope it is resolved soon either way!

hkstemclub, 2021-03-04:
Same problem here, half year before I use the same image in old jetson nano B01 board and it was working well....now I use it in the new board it doesn't work.....

legonger, 2021-03-06:
I have the same problem.
When I put another img file (e.g.  "jetson-nano-jp451-sd-card-image.zip") on to the same SD card, it boot normally.
But I put "jetcard_v0p0p0.zip" on to the same SD card, it does not boot.
Only boot logo "NVIDIA" is displayed repeatedly...

zinwalin, 2021-03-08:
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

same here.  I have two B01 board, the same image doesn't work the same behavior even specs are same.

arickchan, 2021-03-10:
I have tried to buy a new A02 board last week and it's work. So I think the problem is the capability between Jetcard image and the new lot if the B01 boards.

tokk-nv, 2021-03-10:
Hi all,
Can anybody take the debug console log (by following a method introduced in [this Jetsonhacks article](https://www.jetsonhacks.com/2019/10/10/jetson-nano-uart/)) and share with us?

zinwalin, 2021-03-15:
They updated the image last weekend.

On Tue, Mar 9, 2021 at 7:27 PM Graham Hilton ***@***.***>
wrote:

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
--
-- Michael Lin Sent from mobile phone

riaz, 2021-08-13:
Looks like its not resolved yet!

diamondbarcode, 2022-05-04:
is anyone with a sd image that work can be share ? ..

arickchan, 2022-11-25:
@tokk-nv

Hello everyone,

I tried the new image with new version of jetpack, It works perfect in the training notebook.

But when I try the road following program, error message comes with the first code I run:

---------------------------------------------------------------------------
OSError                                   Traceback (most recent call last)
<ipython-input-2-85080642f8f2> in <module>
----> 1 import torch
      2 import torchvision
      3
      4 CATEGORIES = ['apex']
      5

/usr/local/lib/python3.6/dist-packages/torch/__init__.py in <module>
    186     # See Note [Global dependencies]
    187     if USE_GLOBAL_DEPS:
--> 188         _load_global_deps()
    189     from torch._C import *
    190

/usr/local/lib/python3.6/dist-packages/torch/__init__.py in _load_global_deps()
    139     lib_path = os.path.join(os.path.dirname(here), 'lib', lib_name)
    140
--> 141     ctypes.CDLL(lib_path, mode=ctypes.RTLD_GLOBAL)
    142
    143

/usr/lib/python3.6/ctypes/__init__.py in __init__(self, name, mode, handle, use_errno, use_last_error)
    346
    347         if handle is None:
--> 348             self._handle = _dlopen(self._name, mode)
    349         else:
    350             self._handle = handle

OSError: /usr/lib/aarch64-linux-gnu/libgomp.so.1: cannot allocate memory in static TLS block

Any idea to solve the problem? thanks everyone help me.

Rick

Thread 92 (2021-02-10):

SOLVED: Waveshare Jetracer Pro Car motor does not turn on when issuing command from Python lab notebook

tomvolek, 2021-02-10:
HI:  I purchased a Jetracer Pro kit from Waveshare web site directly and followed the configuration to the teeth as stated here:[https://www.waveshare.com/wiki/JetRacer_Pro_AI_Kit](url)  . I am able to connect to Nano board remotely via my laptop ofcourse and connect to the port which Phyton Lab notebook is running.

I have reviewed wiring connection as it is shown in Waveshare  assembly guide ( [https://www.waveshare.com/w/upload/f/fa/Jetracer_pro_Assembly_EN.pdf](url)

However when I run the basic_motion.py  the car motor does not react, I do not hear any noise from the motor, car does not move and steering does not work.

In the basic_motion.ipynb file I execute :
from  jetracer.nvidia_racecar import NvidiaRacecar
car = NvidiaRacecar()
then i see a comment saying : "If the car does not respond, it maybe in manual mode. flip the mnaula switch on teh RC transmitter."    However i don't see a switch or i don't know where it is.

Next I run :
 car.steering = 0.3
print(car.steering_gain)
output: -0.65
print(car.steering_offset)
output: 0.0
car.throttle =0.0

No reaction from the car , no movement.   Any idea what could the problem?

openbsod, 2021-02-18:
Hi.

Probably you may try check your i2c bus?

+-

`
jetson@jetson:~$
jetson@jetson:~$ i2cdetect -l
i2c-3	i2c       	7000c700.i2c                    	I2C adapter
i2c-1	i2c       	7000c400.i2c                    	I2C adapter
i2c-6	i2c       	Tegra I2C adapter               	I2C adapter
i2c-4	i2c       	7000d000.i2c                    	I2C adapter
i2c-2	i2c       	7000c500.i2c                    	I2C adapter
i2c-0	i2c       	7000c000.i2c                    	I2C adapter
i2c-5	i2c       	7000d100.i2c                    	I2C adapter
jetson@jetson:~$
jetson@jetson:~$
jetson@jetson:~$ for i in 0 1 2 6; do i2cdetect -y -r $i; done
     0  1  2  3  4  5  6  7  8  9  a  b  c  d  e  f
00:          -- -- -- -- -- -- -- -- -- -- -- -- --
10: -- -- -- -- -- -- -- -- -- -- -- -- -- -- -- --
20: -- -- -- -- -- -- -- -- -- -- -- -- -- -- -- --
30: -- -- -- -- -- -- -- -- -- -- -- -- -- -- -- --
40: -- -- -- -- -- -- -- -- -- -- -- -- -- -- -- --
50: -- -- -- -- -- -- -- -- -- -- -- -- -- -- -- --
60: -- -- -- -- -- -- -- -- -- -- -- -- -- -- -- --
70: -- -- -- -- -- -- -- --                 
     0  1  2  3  4  5  6  7  8  9  a  b  c  d  e  f
00:          -- -- -- -- -- -- -- -- -- -- -- -- --
10: -- -- -- -- -- -- -- -- -- -- -- -- -- -- -- --
20: -- -- -- -- -- -- -- -- -- -- -- -- -- -- -- --
30: -- -- -- -- -- -- -- -- -- -- -- -- 3c -- -- --
40: 40 -- 42 -- -- -- -- -- -- -- -- -- -- -- -- --
50: -- -- -- -- -- -- -- -- -- -- -- -- -- -- -- --
60: -- -- -- -- -- -- -- -- -- -- -- -- -- -- -- --
70: 70 -- -- -- -- -- -- --                 
     0  1  2  3  4  5  6  7  8  9  a  b  c  d  e  f
00:          -- -- -- -- -- -- -- -- -- -- -- -- --
10: -- -- -- -- -- -- -- -- -- -- -- -- -- -- -- --
20: -- -- -- -- -- -- -- -- -- -- -- -- -- -- -- --
30: -- -- -- -- -- -- -- -- -- -- -- -- -- -- -- --
40: -- -- -- -- -- -- -- -- -- -- -- -- -- -- -- --
50: 50 -- -- -- -- -- -- 57 -- -- -- -- -- -- -- --
60: -- -- -- -- -- -- -- -- -- -- -- -- -- -- -- --
70: -- -- -- -- -- -- -- --                 
     0  1  2  3  4  5  6  7  8  9  a  b  c  d  e  f
00:          -- -- -- -- -- -- -- -- -- -- -- -- --
10: UU -- -- -- -- -- -- -- -- -- -- -- -- -- -- --
20: -- -- -- -- -- -- -- -- -- -- -- -- -- -- -- --
30: -- -- -- -- -- -- -- -- -- -- -- -- -- -- -- --
40: UU -- -- -- -- -- -- -- -- -- -- -- -- -- -- --
50: -- -- -- -- -- -- -- -- -- -- -- -- -- -- -- --
60: -- -- -- -- -- -- -- -- -- -- -- -- -- -- -- --
70: -- -- -- -- -- -- -- --                 
`

I`m also have few problems with JetracerPro but my jetracer gain throttle by itself ( does not respect car.throttle value at all)

BR

tomvolek, 2021-03-02:
openbsod:   This is how it looks for me, exactly as you listed. what are we looking for ?

etson@jetson:~$ i2cdetect -l
i2c-3   i2c             7000c700.i2c                            I2C adapter
i2c-1   i2c             7000c400.i2c                            I2C adapter
i2c-6   i2c             Tegra I2C adapter                       I2C adapter
i2c-4   i2c             7000d000.i2c                            I2C adapter
i2c-2   i2c             7000c500.i2c                            I2C adapter
i2c-0   i2c             7000c000.i2c                            I2C adapter
i2c-5   i2c             7000d100.i2c                            I2C adapter
jetson@jetson:~$ for i in 0 1 2 6; do i2cdetect -y -r $i; done
     0  1  2  3  4  5  6  7  8  9  a  b  c  d  e  f
00:          -- -- -- -- -- -- -- -- -- -- -- -- --
10: -- -- -- -- -- -- -- -- -- -- -- -- -- -- -- --
20: -- -- -- -- -- -- -- -- -- -- -- -- -- -- -- --
30: -- -- -- -- -- -- -- -- -- -- -- -- -- -- -- --
40: -- -- -- -- -- -- -- -- -- -- -- -- -- -- -- --
50: -- -- -- -- -- -- -- -- -- -- -- -- -- -- -- --
60: -- -- -- -- -- -- -- -- -- -- -- -- -- -- -- --
70: -- -- -- -- -- -- -- --
     0  1  2  3  4  5  6  7  8  9  a  b  c  d  e  f
00:          -- -- -- -- -- -- -- -- -- -- -- -- --
10: -- -- -- -- -- -- -- -- -- -- -- -- -- -- -- --
20: -- -- -- -- -- -- -- -- -- -- -- -- -- -- -- --
30: -- -- -- -- -- -- -- -- -- -- -- -- 3c -- -- --
40: 40 -- 42 -- -- -- -- -- -- -- -- -- -- -- -- --
50: -- -- -- -- -- -- -- -- -- -- -- -- -- -- -- --
60: -- -- -- -- -- -- -- -- -- -- -- -- -- -- -- --
70: 70 -- -- -- -- -- -- --
     0  1  2  3  4  5  6  7  8  9  a  b  c  d  e  f
00:          -- -- -- -- -- -- -- -- -- -- -- -- --
10: -- -- -- -- -- -- -- -- -- -- -- -- -- -- -- --
20: -- -- -- -- -- -- -- -- -- -- -- -- -- -- -- --
30: -- -- -- -- -- -- -- -- -- -- -- -- -- -- -- --
40: -- -- -- -- -- -- -- -- -- -- -- -- -- -- -- --
50: 50 -- -- -- -- -- -- 57 -- -- -- -- -- -- -- --
60: -- -- -- -- -- -- -- -- -- -- -- -- -- -- -- --
70: -- -- -- -- -- -- -- --
     0  1  2  3  4  5  6  7  8  9  a  b  c  d  e  f
00:          -- -- -- -- -- -- -- -- -- -- -- -- --
10: UU -- -- -- -- -- -- -- -- -- -- -- -- -- -- --
20: -- -- -- -- -- -- -- -- -- -- -- -- -- -- -- --
30: -- -- -- -- -- -- -- -- -- -- -- -- -- -- -- --
40: UU -- -- -- -- -- -- -- -- -- -- -- -- -- -- --
50: -- -- -- -- -- -- -- -- -- -- -- -- -- -- -- --
60: -- -- -- -- -- -- -- -- -- -- -- -- -- -- -- --
70: -- -- -- -- -- -- -- --
jetson@jetson:~$

zinwalin, 2021-03-15:
Check wires connect servo and motor
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
--
-- Michael Lin Sent from mobile phone

tokk-nv, 2021-03-19:
Hi tomvolek,
Did you turn on the Power SW on the ESC?

In my kit, it is located in the RC vehicle's battery bay, and you need to slide to the left to turn it on.
(Notice the red LED blinking in the back)
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

tomvolek, 2021-03-21:
Thanks @tokk-nv . That was the problem.  I had not seen the black Servo switch and it was off. Embarrassing  :(
Motor now works and I have started experimenting.

Thanks again

tokk-nv, 2021-03-22:
Thank you so much for an update, and I am very glad that you get to now run the vehicle!

Closed 2021-03-21.

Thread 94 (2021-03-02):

jetracer basic motion error

jackey42, 2021-03-02:
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

sudo pip3 install --upgrade pip
sudo pip3 uninstall Adafruit-PureIO
sudo pip3 install Adafruit-PureIO

We already tried this, but the error has not solved.

Please help ;n;

jackey42, 2021-03-10:
Hi~!
I'm using Waveshare JetRacer.

-----Original Message-----
From: "Chitoku YATO"<notifications@github.com>
To: "NVIDIA-AI-IOT/jetracer"<jetracer@noreply.github.com>;
Cc: "jackey42"<jenny_jung@naver.com>; "Author"<author@noreply.github.com>;
Sent: 2021-03-10 (수) 16:19:42 (GMT+09:00)
Subject: Re: [NVIDIA-AI-IOT/jetracer] jetracer basic motion error (#94)

Hi jackey42,
Can you tell me what vehicle hardware you are using?
(Latrax? Tamiya? or Waveshare JetRacer? Waveshare JetRacer Pro?)
—
You are receiving this because you authored the thread.
Reply to this email directly, view it on GitHub, or unsubscribe.

zinwalin, 2021-03-15:
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

use waveshare image，and deploy patches for specific hardware.

tokk-nv, 2021-03-19:
Hi jackey42,

As zinwalin suggested, please check out the Waveshare image which they also posted in this issue here.
https://github.com/NVIDIA-AI-IOT/jetracer/issues/96

openbsod, 2021-04-26:
Hello jackey42

Met same errors with JetRacer Pro. So my conditions are:

- JetRacer Pro https://www.waveshare.com/wiki/JetRacer_Pro_AI_Kit

- jetcard_nano-4gb-jp451 https://doc-0c-bc-docs.googleusercontent.com/docs/securesc/oca2mgdh5rj4h8hbtk0do6b37cs03g8n/rqmq8oajntfduih3euka329cmkam653k/1619391975000/08570363794112935001/15224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

- Jetson Nano (A02) 4GB

- branch ws/pro https://github.com/waveshare/jetracer/tree/ws/pro

With this branch I can get basic motions notebook about fully working execpt backward motion. It can move forward like normal jetracer do, but moves backward with 'donkeycar' scheme 'Reverse on RC cars is a little tricky because the ESC must receive a reverse pulse, zero pulse, reverse pulse to start to go backwards.' as described at https://docs.donkeycar.com/guide/calibrate/

BR, Ed.

Closed 2022-07-18.

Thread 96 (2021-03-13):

Pre-built image (Jetpack4.5) for Waveshare JetRacer Pro AI Kit and JetRacer AI Kit

waveshare, 2021-03-13:
We make a Jetracer Pro image based on Jetpack4.5. If you use Jetson Nano Developer Kit (B01) and the Waveshare JetRacer Pro AI, Kit. You can download this image and test it.
link: https://drive.google.com/file/d/1bgCAUJ9m16g5FGuYgKy3WmGI-pGjPXN0/view?usp=sharing

If you have the JetRacer AI Kit. Please switch the Jetracer repository and reinstall with the following commands:
```
cd jetracer
git checkout master
sudo python3 setup.py install
sudo reboot
```

korzen, 2021-03-26:
@waveshare  sorry, but it is still unclear to me what I should do to get the JetRacer AI Kit (non-pro with Nano A01) up and running. I have burned a fresh JetPack 4.5.1 and manually installed the JetCard from 4.5.1 branch. The thing is that the Jupyter is not starting but that is different story. Which repo/branch should I use to get the RaceCar working with 4.5 update. Thanks

DeepLJoerg, 2021-04-19:
> @waveshare sorry, but it is still unclear to me what I should do to get the JetRacer AI Kit (non-pro with Nano A01) up and running. I have burned a fresh JetPack 4.5.1 and manually installed the JetCard from 4.5.1 branch. The thing is that the Jupyter is not starting but that is different story. Which repo/branch should I use to get the RaceCar working with 4.5 update. Thanks

Did you download the right image? There is one for 2GB and one for 4GB.

diamondbarcode, 2022-05-04:
i am 2nd on this, where is pre-made sd card image for none pro versioin ? ..

waveshare, 2022-05-06:
@diamondbarcode
The non pro version uses the same image as the pro version. The only different is that you need to go into the jetracer directory and swich the batch to master and re-install it.
Please check our wiki for details.

hemnsue, 2023-11-21:
hello waveshare i need your help, kindly reply please ,in my waveshare jet racer ai kit (non pro version) the rear motors are not running they don't respond to the basic motion when i set car.throttle=1 or -1 or anyother value between -1 to 1. My servo motors are running well and good i just needed help in this problem . The car.throttle_gain has been set to 0.8 , but i don't get any kind of response from the dc motors when i run it, servo motors are running good, i have the Jetson Nano B0-1 board and all my connections are correct i have rechecked them many times and also when i'm normally power the motors to check if they are fine using a battery they are running good so there is no problem with the motors in general . Please help . It will be really helpful as i really want to explore and learn about autonomous driving and do some personal projects.

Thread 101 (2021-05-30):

No response to Basic_motion

sdovhl, 2021-05-30:
Hello everyone,

During running through the basic_motion notebook we couldn’t get any response from the car.
The transmitter and reciever we are using is the Carson Reflex PRO 3 (without LCD) the transmitter als isnt equiped with a manual override switch, when self operating the car, everything works just fine however whenever we try to get to run the car through the basic_motion notebook the car doesnt response on any setting we try  (neither steering nor throttle).

We tried to set the throttle_gain to a negative value, which also didnt give any response. We have also tried to bypass the multiplexer and connect the PCA PWM driver tot he ESC directly which also didnt give any response.

The transmitter is equiped with reverse switches which reverse the throttle and steering, while driving the car manually setting the reverse throttle switch to reverse mode will get the car to automatically drive in reverse motion without moving the throttle trigger forward backward. Whilst trying to run the Basic_motion notebook during this mode, we couldnt get any response either.

Thank You in advance for any hints.

sdovhl, 2021-05-30:
We are using the Tamiya jetracer

TCIII, 2021-05-31:
You didn't state what version of Jetracer you are using.
Are you using the Jetracer latest release on a Nano 4GB B01 or an earlier version?

sdovhl, 2021-05-31:
> You didn't state what version of Jetracer you are using.
> Are you using the Jetracer latest release on a Nano 4GB B01 or an earlier version?

We are using the latest version on a Nano 4GB B01 indeed.

TCIII, 2021-05-31:
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

I assume that you used the latest release image and did not build Jetracer from scratch?
Did you take a look at open issue #99 before doing the Jetracer image install? Issue #99 may explain the issues that you are having with "basic_motion".

sdovhl, 2021-05-31:
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

I installed the latest release according to your guide in open issue #99 before installing the Jetracer image, however at step 4 permission is still denied while trying to install Jetcam and Jetracer. Basic motion still gives no response when running it

TCIII, 2021-05-31:
@sdovhl

When you say that you "installed the latest release" are you talking about the Jetracer latest release image?

If so, that is not what I did to get my installation of Jetracer to work. I did a clean install and setup of of Jetpack 4.5.1 and then cloned and installed Jetcard followed by Jetcam and Jetracer.

sdovhl, 2021-05-31:
I followed your steps in issue #99 from start to finish, are there any more steps i had to do beforehand?
As I downloaded the zip file of jp 4.5.1 and transferred it to a micro SD, after that i followed on from step 2 however at step 4 it still kept on saying permission denied when trying to clone the packages.

TCIII, 2021-06-01:
@sdovhl,

I am sorry to hear that my guide has not worked for you.

Somehow you are doing something differently than I did during the installation process and unfortunately I don't know what it is.

sdovhl, 2021-06-01:
When running sudo apt-get upgrade -y, It said some packages couldnt get the upgrade and said i should try  sudo apt-get upgrade --fix-missing, which i did. During the whole process it asked me to update the software (to ubuntu 18.04). It also asked my a question twice which i had to answer (y/N), once for overwriting jupyiter notebook with default Data or something like that which i rejected (N) and the other question was to install an extra package.

Just some things that were noticable, do you know if any of these might have caused the problem or is it better for me to just go with an older version of jp if that would even work?

TCIII, 2021-06-01:
> When running sudo apt-get upgrade -y, It said some packages couldnt get the upgrade and said i should try sudo apt-get upgrade --fix-missing, which i did. During the whole process it asked me to update the software (to ubuntu 18.04). It also asked my a question twice which i had to answer (y/N), once for overwriting jupyiter notebook with default Data or something like that which i rejected (N) and the other question was to install an extra package.
>
> Just some things that were noticable, do you know if any of these might have caused the problem or is it better for me to just go with an older version of jp if that would even work?

Just run sudo apt-get update -y and then sudo apt-get upgrade -y and then do a reboot. Don't worry about the packages that couldn't be upgraded as they usually can't be upgraded with the NVIDIA version of Ubuntu 18.04.  Just follow my installation guide to the letter and you should have a successful install.

sdovhl, 2021-06-09:
When following your guide, I still couldnt get any response out of the car. After the reboot i still get the same error message shown when viewing it on a monitor. Still cant get any motion going when running basic_motion.
I have also tried with jetpack 4.5, but still couldnt get any motion going on.

TCIII, 2021-06-09:
@sdovhl,

FYI

NVIDIA has addressed the issues I pointed out and packaged a [new image](https://forums.developer.nvidia.com/t/issues-setting-up-jetracer-with-the-latest-release-image/178952/7), partly taking my suggested solutions.

sdovhl, 2021-06-10:
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

Yes I saw! But isnt the new image just the 4.5.1? I've tried basic motion with their newest image however still cant get any motion when running through Basic_motion

TCIII, 2021-06-10:
@sdovhl,

The Jetracer "image" is not just JP 4.5.1, but includes Jetcard which builds a lot of packages and dependencies if you run it separately from JP 4.5.1.
Is your jet racer a kit or is it a DIY project?

Have you verified that the Nano is communicating with the PCA9685 servo driver module over the I2C bus?
Run the following to command vis SSH to verify that the Nano is communicating with the PCA9685:

sudo i2cdetect -r -y 1

The PCA9685 should appear at hex address 0x40.

If it appears at the correct hex address, then connect the ESC and steering servo cables directly to the PCA9685 and see if you can get basic_motion to operate the car throttle and steering. If that works, then there is something wrong with the multiplexer or the way that you have attached the throttle/steering cables to it.
If it does not appear at hex address 0x40, then that is where your problem is.

sdovhl, 2021-06-16:
Hi, thank you for your help! We have now solved the issue.
With the new image we tried to bypass the multiplexer (connect the PCA motor driver directly to the ESC) and this time it was succesfull, we were able to run "basic_motion" now.
We have installed a manual override switch on channel 3 of the transmitter and now it works.

Closed 2021-06-16.

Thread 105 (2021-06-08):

No response to basic motions but no errors either

TigroTigro, 2021-06-08:
I've just installed the latest jetracer on my 2GB Jetson Nano creating the card manually through the Jetcard and Jetracer tutorials and everything seems fine, I assembled my Waveshare Jetracer Pro AI Kit, I mounted Jetson on top of it, the fan is working but when I try to go through any of the basic motions, be it through the provided notebooks or on my own through the terminal, nothing happens. Here's the log:

```
>>> from jetracer.nvidia_racecar import NvidiaRacecar
>>>
>>>
>>> car = NvidiaRacecar()
>>> car.steering = 0.3
>>> print(car.steering_gain)
-0.65
>>> print(car.steering_offset)
0.0
>>> car.throttle = 0.2
>>> print(car.throttle_gain)
0.8
>>> car.throttle_gain = 0.5
>>>
```

As you can see, there are no errors but the car stands still. I don't know how I can force it out of the manual (if that even is the problem) cause it does not even seem to be in it as I have not installed the [wireless module antennas](https://www.amazon.com/Waveshare-AC8265-Wireless-Supports-Bluetooth/dp/B07SGDRG34) (as my Nano is not supporting external extension cards) and am instead using a USB network adapter which provides WiFi to the Nano.

How can I make it work?

s95huang, 2021-06-09:
Hi, I had the same problem before. Take it easy~ Here is the solution:

You need to turn on the RC ESC switch hidden under the left WiFi antenna or near the rear left tire to get it to move.\
It took me a while to find the switch so please look carefully.
If done properly, you should hear a  beep and probably see a red light, meaning that the ESC is on

When turning on the fan, the jetson nano could consume more than 5W which is more than what the battery is designed to supply. \
I suggest you to turn it off.

You should be able to install the Wireless NIC Module by removing the jetson nano compute module (aka the card). \
The USB WiFi dongle should work fine.

Please be careful when playing with the throttle value since mine run off the stairs (It didn't break) ...

TigroTigro, 2021-06-09:
Yes, that was it! Thanks so much @s95huang :D

> You should be able to install the Wireless NIC Module by removing the jetson nano compute module (aka the card).
> The USB WiFi dongle should work fine.

Sadly, my version does not feature the connector underneath the module. So while [this](https://docs.nvidia.com/isaac/archive/2019.1/_images/nano-wifi-4.jpg) is what it looks like on many Jetsons, mine has neither that slot nor that screw spot, thus preventing me from installing the module. On a related note, can you use the controller in such a situation or is installing this module crucial for this? Cause right now, I have no way to switch to manual steering and I wonder if that controller needs this module or if it can control the car just fine without it?

Closed 2021-06-09.

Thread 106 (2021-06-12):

Power supply to the Servo Driver

tran9774, 2021-06-12:
Hi guys.

I'm following this build but I didn't purchase a rc controller because I wanted to use my xbox controller for it.
How do you supply power to the PCA9685 to move the Servo?

Greetings from Germany.

akwong922, 2021-06-14:
I did something similar with a PS3 controller. The PCA9685 powers up when connected to the ESC when powered on and i can control the throttle and the steering from it. Not sure if this will cause any problems in the long run though.

tran9774, 2021-06-14:
How did you setup the ESC in that case. Because i don't have a radio transmitter the ESC keeps beeping.
I can control the steering with the Adafruit servo kit library in Python though.

wackerl91, 2021-07-08:
I have pretty much the same setup. Here is what I did:
- Jetson Nano is connected to the PCA9685 using the usual 4-wires connection (powers on with the Jetson)
- Steering servo is connected with all three pins on the PWM headers
- ESC is connected to the PCA9685 using only the PWM signal on the PWM header (not GND/V+, so the Jeston only sends the PWM signal via the PCA9685 board)
- GND/V+ to PCA9685 is supplied from ESC using the green/blue power terminal connector (opposite of the PWM header on the PCA9685 board; not sure if this is strictly necessary as I haven't tried disconnecting those cables)

To my understanding (not an electrics guy ...), this way the servos draw power via the ESC from the car battery instead of from the Jetson - on Adafruit there's a warning that excessive current may cause resets and/or damage when an Arduino provides the power, so I figured the same may be the case for the Jetson.

Regarding the ESC, it beeps as long as no control input has been received. I set both steering servo and motor to 0 when launching my script before switching on the ESC.

Feel free to shoot me a mail if some photos would help you with wiring everything up.

Cheers, and have fun with your Jetracer! :)

dbanshee, 2021-11-18:
Hi guys, building a similar configuration too, I've noticed (at least in my setup) that Voltage on PWM cables from ESC are higher than reasonable 5V. I read 5.9V and this is propagated to PCA9685 and Jetson (really an rpi, but it is not rellevant). So I think this could be dangerous.

I'm not using a battery. I'm using an ATX PSU instead, converting from 12V to 7V with DC-DC stepper down.
Can you check the theorically 5V ESC line with full battery?

I've created a new issue with more details before you are interested.

Grettings from Spain.

Closed 2022-07-18.

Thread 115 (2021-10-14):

How to reverse camera outupt?

haroonhublikar12, 2021-10-14:
I am using imx219 160° camera on my jetracer. I have attached it upside down like everyone else. How can i reverse the camera output? I am getting reversed output in interactive regression.

krissdap, 2021-10-16:
I think the simplest way you can do it is to modify the Jetcam's CSI_Camera
https://github.com/NVIDIA-AI-IOT/jetcam/blob/master/jetcam/csi_camera.py
(do it in your local code)

After each line of
<code>
re, image = self.cap.read()
</code>

you add a line of
<code>
image = cv2.rotate(image, cv2.ROTATE_180)
</code>

which would replace each captured frame with a rotated one.

Closed 2022-01-15.

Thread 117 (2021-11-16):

Jetracer 2GB expansion board

yahya200, 2021-11-16:
I have purchased jeracer 2GB Al kit .
I assembled the hardware by following the instructions in Waveshare wiki , but unfortunately it doesn’t power up and OLED doesn’t display anything when I turn it on. Jetson nano is working properly getting the power from expansion
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
board. What is the problem?please help

Thanks

yongen9696, 2022-05-08:
Hi, I would like to know whether you have solved the issue? My version is a 4GB Pro kit, has the same problem as yours where the OLED display doe not lights up.

K-Molloy, 2022-05-09:
I also have this problem with the 2GB kit, no OLED or motor - but steering is okay

yongen9696, 2022-05-31:
Updates on mine:

1. I have contacted the WaveShare support team, turns out is my expansion board is broken.
2. Bought a new one from their sales team directly, cost me 46.99 USD for the **expansion board only**.

alternative, if you have a device like Arduino, you can DIY with the Jetson nano.

yahya200, 2022-10-11:
https://jetsonhacks.com/2019/12/03/adafruit-pioled-on-jetson-nano/
Hi ,follow steps and enjoy

Sent from my iPhone

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

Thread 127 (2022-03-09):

Trying to create a camera class- getting error message

MaxKru, 2022-03-09:
(https://forums.developer.nvidia.com/t/trying-to-create-a-camera-class-and-getting-this-error-message-could-not-read-image-from-camera/205455/2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)

hello,

im trying to get get a camera working on my jetson nano, waveshare jetracer pro
using the B02 board,

heres my code:
#creating camera class

from jetcam.csi_camera import CSICamera
camera = CSICamera(width=224, height=224, capture_fps=65)

here is my full error output:

RuntimeError Traceback (most recent call last)
/usr/local/lib/python3.6/dist-packages/jetcam-0.0.0-py3.6.egg/jetcam/csi_camera.py in init(self, *args, **kwargs)
23 if not re:
—> 24 raise RuntimeError(‘Could not read image from camera.’)
25 except:

RuntimeError: Could not read image from camera.

During handling of the above exception, another exception occurred:

RuntimeError Traceback (most recent call last)
in
1 from jetcam.csi_camera import CSICamera
2
----> 3 camera = CSICamera(width=224, height=224, capture_fps=65)

/usr/local/lib/python3.6/dist-packages/jetcam-0.0.0-py3.6.egg/jetcam/csi_camera.py in init(self, *args, **kwargs)
25 except:
26 raise RuntimeError(
—> 27 ‘Could not initialize camera. Please see error trace.’)
28
29 atexit.register(self.cap.release)

RuntimeError: Could not initialize camera. Please see error trace.

anybody got an idea how to fix this issue?

hs2415, 2022-08-19:
Hi,
 I'm having the same error in a different project (DLI Getting Started with AI Course) and haven't solved it with the methods I find on NVIDIA. Did you solve it in your case?

Out of curiosity, do you have "jetcam-0.0.0-py3.6.egg/jetcam/csi_camera.py" located in /usr/local/lib/python3.6/dist-packages/? I don't and I wonder if it's related to the error. Hope I'm allowed to ask here!

MaxKru, 2022-08-22:
there is a camera reset service that should do the trick but didnt work for me,
https://github.com/NVIDIA-AI-IOT/jetracer/blob/master/notebooks/reset_camera_service.ipynb
my solution which didnt fix the problem but is a work around, is to restart the jetson nano.
here is another solution you can try, https://github.com/NVIDIA-AI-IOT/jetracer/issues/104

kumar132002, 2024-08-09:
I am stuck with the same issue and have tried reset_camera_service.ipynb ,Are there any other solutions

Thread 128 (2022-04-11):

tegra-i2c pio timed out

nighi, 2022-04-11:
Hi,
I have a waveshare JetRacer AI Kit 4GB, set up with the newest image from this repo and the jetracer repo from the [waveshare fork](https://github.com/waveshare/jetracer).

I can control `steering` and `throttle` from the `basic_motion` notebook, but often a few seconds after activating the motors, the car dies.
No hdmi output, black oLed and not reachable neither via jupyter nor via ssh, but the fan is still spinning.
The behavior doesn't change with or without power supply, and I couldn't reproduce it in response to a special action.
Sometimes it occurs right after setting throttle, sometimes the car drives for a couple seconds.

Something I noticed is that running the car constructor seems to last very long.
```python
car = NvidiaRacecar(steering_channel=0, throttle_channel=0)
```

And after looking at `\var\log\syslog` I get following lines:

```
jetson@nano-4gb-jp451:~$ tail -f /var/log/syslog
Apr  5 04:12:24 nano-4gb-jp451 sh[4210]: [I 04:12:24.101 LabApp] Kernel started: 4a01fbe1-f89c-4030-bfd1-4afd096486af, name: python3
Apr  5 04:12:37 nano-4gb-jp451 kernel: [  227.701164] tegra-i2c 7000c400.i2c: pio timed out addr: 0x40 tlen:0 rlen:0
Apr  5 04:12:37 nano-4gb-jp451 kernel: [  227.709166] tegra-i2c 7000c400.i2c: --- register dump for debugging ----
Apr  5 04:12:37 nano-4gb-jp451 kernel: [  227.716101] tegra-i2c 7000c400.i2c: I2C_CNFG - 0x22c00
Apr  5 04:12:37 nano-4gb-jp451 kernel: [  227.721353] tegra-i2c 7000c400.i2c: I2C_PACKET_TRANSFER_STATUS - 0x10001
Apr  5 04:12:37 nano-4gb-jp451 kernel: [  227.729186] tegra-i2c 7000c400.i2c: I2C_FIFO_CONTROL - 0xe0
Apr  5 04:12:37 nano-4gb-jp451 kernel: [  227.734824] tegra-i2c 7000c400.i2c: I2C_FIFO_STATUS - 0x800080
Apr  5 04:12:37 nano-4gb-jp451 kernel: [  227.740796] tegra-i2c 7000c400.i2c: I2C_INT_MASK - 0x7c
Apr  5 04:12:37 nano-4gb-jp451 kernel: [  227.746138] tegra-i2c 7000c400.i2c: I2C_INT_STATUS - 0x2
Apr  5 04:12:37 nano-4gb-jp451 kernel: [  227.751491] tegra-i2c 7000c400.i2c: i2c transfer timed out addr: 0x40
Apr  5 04:12:48 nano-4gb-jp451 kernel: [  237.940955] tegra-i2c 7000c400.i2c: pio timed out addr: 0x60 tlen:0 rlen:0
Apr  5 04:12:48 nano-4gb-jp451 kernel: [  237.948888] tegra-i2c 7000c400.i2c: --- register dump for debugging ----
Apr  5 04:12:48 nano-4gb-jp451 kernel: [  237.956871] tegra-i2c 7000c400.i2c: I2C_CNFG - 0x22c00
Apr  5 04:12:48 nano-4gb-jp451 kernel: [  237.962429] tegra-i2c 7000c400.i2c: I2C_PACKET_TRANSFER_STATUS - 0x10001
Apr  5 04:12:48 nano-4gb-jp451 kernel: [  237.970505] tegra-i2c 7000c400.i2c: I2C_FIFO_CONTROL - 0xe0
Apr  5 04:12:48 nano-4gb-jp451 kernel: [  237.976860] tegra-i2c 7000c400.i2c: I2C_FIFO_STATUS - 0x800080
Apr  5 04:12:48 nano-4gb-jp451 kernel: [  237.982922] tegra-i2c 7000c400.i2c: I2C_INT_MASK - 0x7c
Apr  5 04:12:48 nano-4gb-jp451 kernel: [  237.988274] tegra-i2c 7000c400.i2c: I2C_INT_STATUS - 0x2
Apr  5 04:12:48 nano-4gb-jp451 kernel: [  237.993738] tegra-i2c 7000c400.i2c: i2c transfer timed out addr: 0x60

```
This can be reproduced every time the `NvidiaRacecar` constructor is called, and the message is always the same (Address 0x40 and 0x60).

Running

```sudo i2cdetect -y -r 1```

returns
```
     0  1  2  3  4  5  6  7  8  9  a  b  c  d  e  f
00:          -- -- -- -- -- -- -- -- -- -- -- -- --
10: -- -- -- -- -- -- -- -- -- -- -- -- -- -- -- --
20: -- -- -- -- -- -- -- -- -- -- -- -- -- -- -- --
30: -- -- -- -- -- -- -- -- -- -- -- -- 3c -- -- --
40: 40 41 -- -- -- -- -- -- -- -- -- -- -- -- -- --
50: -- -- -- -- -- -- -- -- -- -- -- -- -- -- -- --
60: 60 -- -- -- -- -- -- -- -- -- -- -- -- -- -- --
70: 70 -- -- -- -- -- -- --                 
```
which seems okay for my understanding.

Thank you for any help!

JihunDev, 2023-06-15:
Hi @nighi Same issue occurred. If you solve it, please share.

nighi, 2023-06-15:
Puh, unfortunately I haven't access to a jetracer anymore.
If I remember it correctly I could fix this issue by choosing a different version of the image. But don't ask me which version has worked. Sorry

KSU-Chad, 2023-11-08:
Similar issue, cannot find I2C device 0x60
`from jetracer.nvidia_racecar import NvidiaRacecar

car = NvidiaRacecar()`
results in Timeout Error

`---------------------------------------------------------------------------
TimeoutError                              Traceback (most recent call last)
/usr/local/lib/python3.6/dist-packages/adafruit_circuitpython_busdevice-5.0.6-py3.6.egg/adafruit_bus_device/i2c_device.py in __probe_for_device(self)
    153         try:
--> 154             self.i2c.writeto(self.device_address, b"")
    155         except OSError:

/usr/local/lib/python3.6/dist-packages/Adafruit_Blinka-6.10.0-py3.6.egg/busio.py in writeto(self, address, buffer, start, end, stop)
    157             return self._i2c.writeto(address, memoryview(buffer)[start:end], stop=stop)
--> 158         return self._i2c.writeto(address, buffer, stop=stop)
    159

/usr/local/lib/python3.6/dist-packages/Adafruit_Blinka-6.10.0-py3.6.egg/adafruit_blinka/microcontroller/generic_linux/i2c.py in writeto(self, address, buffer, start, end, stop)
     48             end = len(buffer)
---> 49         self._i2c_bus.write_bytes(address, buffer[start:end])
     50

/usr/local/lib/python3.6/dist-packages/Adafruit_PureIO-1.1.8-py3.6.egg/Adafruit_PureIO/smbus.py in write_bytes(self, addr, buf)
    307         self._select_device(addr)
--> 308         self._device.write(buf)
    309

TimeoutError: [Errno 110] Connection timed out

During handling of the above exception, another exception occurred:

OSError                                   Traceback (most recent call last)
/usr/local/lib/python3.6/dist-packages/adafruit_circuitpython_busdevice-5.0.6-py3.6.egg/adafruit_bus_device/i2c_device.py in __probe_for_device(self)
    159                 result = bytearray(1)
--> 160                 self.i2c.readfrom_into(self.device_address, result)
    161             except OSError:

/usr/local/lib/python3.6/dist-packages/Adafruit_Blinka-6.10.0-py3.6.egg/busio.py in readfrom_into(self, address, buffer, start, end)
    147         stop = True  # remove for efficiency later
--> 148         return self._i2c.readfrom_into(address, buffer, stop=stop)
    149

/usr/local/lib/python3.6/dist-packages/Adafruit_Blinka-6.10.0-py3.6.egg/adafruit_blinka/microcontroller/generic_linux/i2c.py in readfrom_into(self, address, buffer, start, end, stop)
     55
---> 56         readin = self._i2c_bus.read_bytes(address, end - start)
     57         for i in range(end - start):

/usr/local/lib/python3.6/dist-packages/Adafruit_PureIO-1.1.8-py3.6.egg/Adafruit_PureIO/smbus.py in read_bytes(self, addr, number)
    178         self._select_device(addr)
--> 179         return self._device.read(number)
    180

OSError: [Errno 121] Remote I/O error

During handling of the above exception, another exception occurred:

ValueError                                Traceback (most recent call last)
<ipython-input-3-2b783e4b0c4f> in <module>
      1 from jetracer.nvidia_racecar import NvidiaRacecar
      2
----> 3 car = NvidiaRacecar()

/usr/local/lib/python3.6/dist-packages/jetracer-0.0.0-py3.6.egg/jetracer/nvidia_racecar.py in __init__(self, *args, **kwargs)
     16         super(NvidiaRacecar, self).__init__(*args, **kwargs)
     17         self.kit = ServoKit(channels=16, address=self.i2c_address1)
---> 18         self.motor = ServoKit(channels=16, address=self.i2c_address2)
     19         self.motor._pca.frequency = 1600
     20         self.steering_motor = self.kit.continuous_servo[self.steering_channel]

/usr/local/lib/python3.6/dist-packages/adafruit_circuitpython_servokit-1.3.4-py3.6.egg/adafruit_servokit.py in __init__(self, channels, i2c, address, reference_clock_speed, frequency)
     79             i2c = board.I2C()
     80         self._pca = PCA9685(
---> 81             i2c, address=address, reference_clock_speed=reference_clock_speed
     82         )
     83         self._pca.frequency = frequency

/usr/local/lib/python3.6/dist-packages/adafruit_circuitpython_pca9685-3.3.6-py3.6.egg/adafruit_pca9685.py in __init__(self, i2c_bus, address, reference_clock_speed)
    118
    119     def __init__(self, i2c_bus, *, address=0x40, reference_clock_speed=25000000):
--> 120         self.i2c_device = i2c_device.I2CDevice(i2c_bus, address)
    121         self.channels = PCAChannels(self)
    122         """Sequence of 16 `PWMChannel` objects. One for each channel."""

/usr/local/lib/python3.6/dist-packages/adafruit_circuitpython_busdevice-5.0.6-py3.6.egg/adafruit_bus_device/i2c_device.py in __init__(self, i2c, device_address, probe)
     48
     49         if probe:
---> 50             self.__probe_for_device()
     51
     52     def readinto(self, buf, *, start=0, end=None):

/usr/local/lib/python3.6/dist-packages/adafruit_circuitpython_busdevice-5.0.6-py3.6.egg/adafruit_bus_device/i2c_device.py in __probe_for_device(self)
    161             except OSError:
    162                 # pylint: disable=raise-missing-from
--> 163                 raise ValueError("No I2C device at address: 0x%x" % self.device_address)
    164                 # pylint: enable=raise-missing-from
    165         finally:

ValueError: No I2C device at address: 0x60`

chentyra, 2024-04-02:
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

I got the same error before updating the pre-installed repository. I have updated the package following the instructions on the Waveshare website:

```
cd jetracer
git checkout ws/pro
sudo python3 setup.py install
```
After these steps the problem no longer occurred.

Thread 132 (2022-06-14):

Tamiya TT-02 Jetracer isn't moving, issue seems to be the multiplexer

ParkerAI, 2022-06-14:
Got the Tamiya built and mounted, but having issues getting it moving.

I've managed to, I believe, isolate the problem to the multiplexer. When routed through there none of the notebooks will execute. Plugging into the PG directly allows for both movement and rotation, so that seems to be the a pretty clear indication of the fault.

Issue is, I'm not familiar enough with the hardware to simply conclude the multiplexer is bad, or if this is something I can resolve myself. Are there any methods of diagnosis I can use to see if the multiplexer is simply bad or if the issue is somewhere in my build?

gitnabeshin, 2022-06-14:
Hi, I build my jetracer like this fig. without the multiplexer.

https://qiita.com/Nabeshin/items/99ddcdf8e6a4038e5844#車体の組み立て

The multiplexer is just a switcher between 2 signals of RC and Jetson Nano.
This makes jetracer simply and safely work with Jetson Nano and just for steering controlled by ML.
(You must control jetracer forward and backward with RC)

I hope you can make it clear your multiplexer is bad or not.

ParkerAI, 2022-06-22:
Managed to get it figured out and it's moving now, thank you for the response. Turns out I just forgot to flip the override out of manual like an idiot.

coltonwestern, 2024-02-21:
Hi @ParkerAI could you clarify what it means to "flip the override out of manual"? I cam across that while running the first basic motion notebook and am having trouble figuring that out.

CHPA6244, 2024-02-21:
I'm sorry, it's been quite a while and I do not remember exactly what I did. I'll try and remember tomorrow, but the only thing I can recall here was that it was a switch on the radio controller that toggled control between it and the code. It's been so long I can't swear to that being the solution however. I do recall that it was a silly, simple solution, nothing to do with my wiring or system.

Closed 2022-06-22.

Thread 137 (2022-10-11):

Rear motors not working

Rogerval02, 2022-10-11:
When I use the notebooks, the steering is completly fine, but the throttle doesn't respond, no movement, no noise, but I applied Voltage directly to the motors and they work

hemnsue, 2023-11-21:
hello i have the same issue , how did you solve this problem???
Please respond as it will be really helpful, i'm using the waveshare jet racer kit

hemnsue, 2023-11-21:
Please respond please

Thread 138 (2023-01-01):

interactive_regression.ipynb, 'DenseNet' object has no attribute 'num_features'

chentyra, 2023-01-01:
I tried to run interactive_regression.ipynb using Densenet. I get the following error message

```
---------------------------------------------------------------------------
ModuleAttributeError                      Traceback (most recent call last)
<ipython-input-4-08299e61f775> in <module>
     24 # DENSENET 121
     25 model = torchvision.models.densenet121(pretrained=True)
---> 26 model.classifier = torch.nn.Linear(model.num_features, output_dim)
     27
     28 model = model.to(device)

/usr/local/lib/python3.6/dist-packages/torch/nn/modules/module.py in __getattr__(self, name)
    770                 return modules[name]
    771         raise ModuleAttributeError("'{}' object has no attribute '{}'".format(
--> 772             type(self).__name__, name))
    773
    774     def __setattr__(self, name: str, value: Union[Tensor, 'Module']) -> None:

ModuleAttributeError: 'DenseNet' object has no attribute 'num_features'
---------------------------------------------------------------------------
```
when I run this cell:
```
import torch
import torchvision

device = torch.device('cuda')
output_dim = 2 * len(dataset.categories)  # x, y coordinate for each category

# ALEXNET
#model = torchvision.models.alexnet(pretrained=True)
#model.classifier[-1] = torch.nn.Linear(4096, output_dim)

# SQUEEZENET
#model = torchvision.models.squeezenet1_1(pretrained=True)
#model.classifier[1] = torch.nn.Conv2d(512, output_dim, kernel_size=1)
#model.num_classes = len(dataset.categories)

# RESNET 18
#model = torchvision.models.resnet18(pretrained=True)
#model.fc = torch.nn.Linear(512, output_dim)

# RESNET 34
#model = torchvision.models.resnet34(pretrained=True)
#model.fc = torch.nn.Linear(512, output_dim)

# DENSENET 121
model = torchvision.models.densenet121(pretrained=True)
model.classifier = torch.nn.Linear(model.num_features, output_dim)

model = model.to(device)

model_save_button = ipywidgets.Button(description='save model')
model_load_button = ipywidgets.Button(description='load model')
model_path_widget = ipywidgets.Text(description='model path', value='road_following_model.pth')

def load_model(c):
    model.load_state_dict(torch.load(model_path_widget.value))
model_load_button.on_click(load_model)

def save_model(c):
    torch.save(model.state_dict(), model_path_widget.value)
model_save_button.on_click(save_model)

model_widget = ipywidgets.VBox([
    model_path_widget,
    ipywidgets.HBox([model_load_button, model_save_button])
])

display(model_widget)
```

chentyra, 2023-01-31:
Densenet121's model, as reported in the file describing net(densenet.py in the folder models of torchvision), does not have any attribute called num_feature( maybe init_num_features). I resolved the problem in two ways:

1. I removed the istruction that defines the classifier.
2. I indicate hardcoded model.num_features. The chosen value was 1024.

chentyra, 2023-01-31:
Densenet121's model, as reported in the file describing net(densenet.py in the folder models of torchvision), does not have any attribute called num_feature( maybe init_num_features). I resolved the problem in two ways:

I removed the istruction that defines the classifier.
I indicated hardcoded model.num_features. The chosen value was 1024.

Closed 2023-01-31.

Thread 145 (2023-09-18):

Jetracer Road Following Live Demo Does Nothing

CamRoni1339, 2023-09-18:
After running through basic motions and the interactive trainer (training 150 images and 20 or so epochs) (both notebooks working) I save it to the path road_following_model.pth, run through the road following notebook and nothing happens. It just drives straight, not adjusting for the track at all. It is almost as if the training is not working and it is just running through basic motions (even though I shut down that notebook). I tested the model live with the blue circle and it is predicting the correct spots, just not doing anything in the road following notebook. I have tried re-training it with new data but I can’t seem to get anything to work. I’m not sure if I am doing something wrong, if it is a hardware issue, or a software issue.

Help would be much appreciated

Thank you

jaybdub, 2023-09-18:
Thanks for reaching out.

If the model is predicting the circle correctly, it's likely the issue may not be with the model itself, but with the code used to convert the detection into a control command.

Is the steering working properly with the other notebooks?

One thing that may help test, is to disable the throttle, and hold the racer an inch or two above the track, tilting it side to side.  If it's working properly you should see the steering wheels turn in a way that makes sense.  If perhaps, the steering is inverted or has a large delay, this could help identify that problem.

Hope this helps, let me know if you have any questions.

John

CamRoni1339, 2023-09-18:
The steering was working properly in the previous notebooks (after some troubleshooting issues). I don't think its a problem with the car, it seems as if it's just not using the trained data.

CamRoni1339, 2023-09-19:
@jaybdub Do you have any other suggestions? I've been stuck on this for a while and would really appreciate it.

jaybdub, 2023-09-19:
Hi @CamRoni1339 ,

It may be good to try the original PyTorch model, to eliminate the possibility that there is an issue when using the optimized TensorRT model.

Could you try using the original model PyTorch model (like that at the top of the optimize_model notebook) inside the road following notebook to check if this works?

Best,
John

CamRoni1339, 2023-09-20:
Hi @jaybdub

BTW I would like to have it be known that I am very new to this kind of stuff and this is my first project like this. I thought it would be a cool high school project to pick up, but as you can tell I have run into some problems.

I tried running it with the original model and saw no difference. I will list the steps that I went through just to make sure that I did it correctly.

1. I ran these two blocks
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

2. I then skipped over these 3 (because they used the optimized model)
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

3. And then I ran these 2
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

4. And finally ran the last one
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

The car still just moves straight with no signs that it is trying to stay on the track. It could be something very simple such as a wrong piece of code, but I am not getting any errors, which just makes this harder. Is there anything I can do to validate the code is loading and running the trained model? I really appreciate all your help.

Thank you so much,
Cameron

CamRoni1339, 2023-10-01:
@jaybdub

After working on and figuring out some things, I have solved some problems, but some are still there.

I decided to start over and re-flash the software on a new sd card to make sure that I hadn't messed up any code. After running through the basic motions, training 250 pictures for 15 epochs, and then running the road following notebook, the results are different. The car is still not able to stay on the track properly, but it now shows signs of trying to turn instead of just driving straight. I have looked at the evaluation and the blue dot is in the correct places, it is just still not working in the road following.

Any help would be much appreciated.

Thanks, Cameron

CamRoni1339, 2023-10-12:
SOLUTION

The car.steering_gain value is set by default to -0.65 and you need to set that back to positive. Because of the way the equation is set up the steering will always be backwards of what you want it to be (this was why my car was not following the training. It was trying to, but the gain was making it go the opposite direction). Once you are able to set the steering_gain to positive the car should work normally.

Closed 2023-10-12.

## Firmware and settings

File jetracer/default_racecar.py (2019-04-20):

from .racecar import Racecar
import traitlets
from adafruit_servokit import ServoKit
from jetmotor.adafruit_servokit_motor import AdafruitServoKitMotor
from jetcam.imx219 import IMX219


class DefaultRacecar(Racecar):
    def __init__(self, *args, **kwargs):
        kit = ServoKit(channels=16)
        self.steering_motor = AdafruitServoKitMotor(kit=kit, channel=0)
        self.throttle_motor = AdafruitServoKitMotor(kit=kit, channel=1)
        
        # link throttle
        traitlets.dlink((self, 'throttle'), (self.throttle_motor, 'value'), transform=lambda x: -x)
        traitlets.dlink((self.throttle_motor, 'value'), (self, 'throttle'), transform=lambda x: -x)
        
        # link steering
        traitlets.link((self, 'steering'), (self.steering_motor, 'value'))

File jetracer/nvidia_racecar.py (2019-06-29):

from .racecar import Racecar
import traitlets
from adafruit_servokit import ServoKit


class NvidiaRacecar(Racecar):
    
    i2c_address = traitlets.Integer(default_value=0x40)
    steering_gain = traitlets.Float(default_value=-0.65)
    steering_offset = traitlets.Float(default_value=0)
    steering_channel = traitlets.Integer(default_value=0)
    throttle_gain = traitlets.Float(default_value=0.8)
    throttle_channel = traitlets.Integer(default_value=1)
    
    def __init__(self, *args, **kwargs):
        super(NvidiaRacecar, self).__init__(*args, **kwargs)
        self.kit = ServoKit(channels=16, address=self.i2c_address)
        self.steering_motor = self.kit.continuous_servo[self.steering_channel]
        self.throttle_motor = self.kit.continuous_servo[self.throttle_channel]
    
    @traitlets.observe('steering')
    def _on_steering(self, change):
        self.steering_motor.throttle = change['new'] * self.steering_gain + self.steering_offset
    
    @traitlets.observe('throttle')
    def _on_throttle(self, change):
        self.throttle_motor.throttle = change['new'] * self.throttle_gain

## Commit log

2019-04-13 live demo steering opt
2019-05-21 removed motor
2019-06-26 :nvidia bom hardware
2019-06-26 Update bill_of_materials.md
    add RC car to BOM
2019-06-29 Add servo extension cables, jumper cap, and jumper wires.
2019-06-29 Add STL files for JetRacer Latrax version
    [JetRacer_Latrax_camera_mount_60mm.stl, JetRacer_Latrax_chassis.stl]
2019-06-29 Add IGES files
    [JetRacer_Latrax_all.iges, JetRacer_Latrax_camera_mount.iges, JetRacer_Latrax_chassis.iges]
2019-06-29 Add STEP files
    [JetRacer_Latrax_all.step, JetRacer_Latrax_camera_mount.step, JetRacer_Latrax_chassis.step]
2019-06-29 Add the F3D file
    [JetRacer_Latrax_all.f3d]
2019-06-29 Rename file names
    [JetRacer_Latrax_all.iges, JetRacer_Latrax_all.step, JetRacer_Latrax_camera_mount.iges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]
2019-07-17 Fix a type in the PWM breakout board Amazon link.
2019-07-29 Move existing Latrax hardware based files under latrax dirs
    [jetracer_latrax_all_parts.f3d, jetracer_latrax_all_parts.iges, jetracer_latrax_all_parts.step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]
2019-07-30 Create BoM doc for Tamiya TT02 chassis
2019-07-30 Update BoM doc for Tamiya TT02
2019-07-30 Move common camera mount CAD files
    [jetracer_cam_mount.iges, jetracer_cam_mount.step, jetracer_cam_mount.stl]
2019-07-30 Fix Latrax STL file links
2019-07-30 Add Tamiya TT02 related STL files and fix links to them
    [jetracer_tamiya_tt02_base_board.stl, jetracer_tamiya_tt02_drill_jig.stl.stl]
2019-07-30 Fix file name error
    [jetracer_tamiya_tt02_drill_jig.stl]
2019-07-31 Add servo, RC battery and charger
2019-08-09 Fix links to STL files
2019-08-12 Update the latrax base-board STL file
    [jetracer_latrax_base_board.stl]
2019-08-12 Update other CAD files for base plate with slit
    [jetracer_latrax_all_parts.f3d, jetracer_latrax_all_parts.iges, jetracer_latrax_all_parts.step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]
2019-10-07 Update CAD files for Tamiya
    Updated to 09-18 version, with reinforced antenna mounts
    [jetracer_tamiya_tt02_base_board.iges, jetracer_tamiya_tt02_base_board.step, jetracer_tamiya_tt02_base_board.stl]
2019-10-07 Update CAD files for Latrax
    Update to 09-20 version, with mounting holes adjusted for easy removal without taking of Jetson Nano Dev Kit.
    [jetracer_latrax_all_parts.f3d, jetracer_latrax_all_parts.iges, jetracer_latrax_all_parts.step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]
2019-10-16 Added new camera mount and store links
    [jetracer_cam_mount.iges, jetracer_cam_mount.step, jetracer_cam_mount.stl]
2019-10-16 updated camera mount for printabiltiy
    [jetracer_cam_mount.stl]
2020-01-29 Update USB powerbank link
    Change the Amazon link of USB powerbank
